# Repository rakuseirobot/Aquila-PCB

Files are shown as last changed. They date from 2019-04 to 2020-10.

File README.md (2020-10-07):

# Aquila-PCB
Aquilaの2019年度、2018年度、回路図及びボード図です。

Robocup Junior Rescue Maze Program

このリポジトリは2019年度のAquilaのメインプログラムです。

# Note

メイン基板のデータです。

/2018以下のAquila-2018-Under基板にセンサーを配線し、メイン基板に配線します。

# Link

[About robot](https://qiita.com/Shunk_/items/b6b5c49862ec9f9d852b)

[How to make RCJM](https://qiita.com/Shunk_/items/2ea0795d571d771d52ca)

[回路](https://github.com/rakuseirobot/Aquila-PCB)

[STM32-program](https://github.com/rakuseirobot/Aquila-2019)

[OpenMV](https://github.com/rakuseirobot/Aquila-OpenMV)

[設計図](https://github.com/rakuseirobot/Aquila-drawings)

[古いメインプログラム(ATxmega)](https://github.com/rakuseirobot/Aquila-Code-v3)

# Author

* Shun Kayaki

    Kyushu institute of Technology
    
    shun@guetan.dev

* Emile

# License

Copyright (c) 2019 Aquila
Released under the MIT license

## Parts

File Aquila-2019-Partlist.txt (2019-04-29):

Partlist

Exported from Aquila-2019-ex.brd at 2019/03/31 14:46

EAGLE Version 9.2.1 Copyright (c) 1988-2018 Autodesk, Inc.

Assembly variant: 

Part           Value                  Package                      Library               Position (mil)        Orientation

3.3C1          100u                   D/7343-31R                   rcl                   (1089.75 3078.75)     R180
3.3C2          0.1u                   C0805                        rcl                   (1163.75 2907.25)     R0
3.3REG         OKL-T_6-W12N-C         OKL-T/3-W5                   SamacSys_Parts        (1300 3900)           R90
5C1            100u                   D/7343-31R                   rcl                   (1841 3094.5)         R180
5C2            0.1u                   C0805                        rcl                   (1671 3223)           R180
5VREG          OKL-T_6-W12N-C         OKL-T/3-W5                   SamacSys_Parts        (2050 3900)           R90
8MHZ           P-08669_HUSG-12.000-20 HC49U-V                      Akizuki               (2625 2281.25)        R0
9C1            100u                   D/7343-31R                   rcl                   (726.25 2809)         R180
9C2            0.1u                   C0805                        rcl                   (832 3075.25)         R0
BOOT0-STM      DTS-6                  DTS-6                        forprint              (1750 662.5)          R180
C1             22uF25V                C2012                        resistor              (1476 3329)           R270
C2             10uF10V                C2012                        resistor              (1675 3355)           R180
C3             22uF25V                C2012                        resistor              (828 3284)            R0
C4             10uF10V                C2012                        resistor              (1000 3341)           R0
C5             22pF                   C1608                        resistor              (2687.5 2425)         R0
C6             22pF                   C1608                        resistor              (2562.5 2425)         R180
CHECKLED       OSTA71A1D-A            OSTA71A1D-A                  FullColorLed-forprint (1450 1787.5)         R270
CON1           XH-4                   CON4                         0@Mylibrary-main1     (3037.5 1356.25)      MR180
CON2           XH-4                   CON4                         0@Mylibrary-main1     (3037.5 1143.75)      MR180
DIO0-JP        BOOT0                  SJ                           jumper                (312.5 856.25)        R90
DIO1-JP        NRST                   SJ                           jumper                (406.25 856.25)       R90
ERROR1-R       330                    R0805                        0@Mylibrary-main1     (950 2400)            MR90
ERROR2-R       330                    R0805                        0@Mylibrary-main1     (950 2100)            MR90
FET1           IRF740                 TO220BV                      transistor-power      (2532 3634)           R0
FET1-R1        100                    R0805                        0@Mylibrary-main1     (2512 3384)           R270
FET1-R2        4.7K                   R0805                        0@Mylibrary-main1     (2432 3384)           R90
FET2           IRF740                 TO220BV                      transistor-power      (3380.5 3722.25)      R180
FET2-R1        100                    R0805                        0@Mylibrary-main1     (3405.75 3652.75)     R270
FET2-R2        4.7K                   R0805                        0@Mylibrary-main1     (3482 3652.75)        R90
GND-CH         GND                    SMD2,54-5,08                 wirepad               (400 1200)            R180
GND-CHK        GND                    2,15/1,0                     wirepad               (1400 1000)           R0
GND-CHK1       GND                    2,15/1,0                     wirepad               (1150 2650)           R0
IC1            STM32F429VGT           LQFP100                      micro-stm_v3          (2600 1800)           R180
IC2            ULN2003AN              DIL16                        ULN2003A              (1750 2500)           R90
IC3            AT24CP                 DIL08                        atmel                 (2150 2500)           R270
IC4            AE-AQM0802             AE-AQM0802                   AE-AQM0802            (3418.75 2931.25)     R90
IIC-R          XH-4                   CON4                         0@Mylibrary-main1     (1350 1300)           R180
INDILED1       330                    R0805                        0@Mylibrary-main1     (1200 2150)           R180
INDILED2       330                    R0805                        0@Mylibrary-main1     (1200 2250)           R180
INDILED3       330                    R0805                        0@Mylibrary-main1     (1200 2350)           R180
INDILED4       330                    R0805                        0@Mylibrary-main1     (1200 2450)           R180
J1             XH-5                   CON5                         0@Mylibrary-main1     (1450 2250)           MR90
JY901          XH-4                   CON4                         0@Mylibrary-main1     (1531.25 1525)        R180
L3             E1                     LED5MM                       0led                  (1000 2500)           R180
L4             E2                     LED5MM                       0led                  (1000 2200)           R180
LED1           OSL10564-CD4026B-R     DIPS1524W50P254L1260H800Q10N OSL10564-CD4026B-R    (3337.5 637.5)        R180
LED2           OSL10564-CD4026B-R     DIPS1524W50P254L1260H800Q10N OSL10564-CD4026B-R    (3337.5 118.75)       R180
LEDSP          MAIN                   AK500/2                      con-ptr500            (2541 3779)           R0
LEDSP2         MAIN                   AK500/2                      con-ptr500            (2946 3779)           R0
M-SW           TL36PO                 TL3XPO                       switch                (600 1200)            R180
MAIN-SPL       XH-2                   CON2                         forprint              (550 2100)            MR180
MAINSW2        MAIN                   MA03-1                       0con-lstb             (243 2718)            R90
MOTORDRIVER    MDCON                  ML14                         0con-harting-ml       (2050 1250)           MR0
Q3             IRF9530                TO220BV                      transistor-power      (550 3300)            R0
Q4             IRF9530                TO220BV                      transistor-power      (355 1725)            R90
Q5             IRF9530                TO220BV                      transistor-power      (550 3100)            R0
R-B            ?                      R0805                        0@Mylibrary-main1     (1700 1750)           MR0
R-G            ?                      R0805                        0@Mylibrary-main1     (1700 1850)           MR0
R-R            ?                      R0805                        0@Mylibrary-main1     (1700 1950)           MR0
R1             1.2k                   0204/7                       resistor              (1858 3291)           R0
R2             1.2k                   0204/7                       resistor              (1143 3262)           R0
RESET-STM      DTS-6                  DTS-6                        forprint              (1750 925)            R180
S1             SKRPACE010             SW_SKRPACE010                SKRPACE010            (1475 475)            R180
S2             VM                     M251                         switch                (2461 3160)           R180
S3             SKRPACE010             SW_SKRPACE010                SKRPACE010            (3568.75 500)         R180
SG1            F/EE17P                F/EE17P                      buzzer                (932 1702)            R270
SL-R1          1K                     R0805                        0@Mylibrary-main1     (2096 3251)           R270
SP-LED                                CHIPLED_0805                 led                   (2096 3090)           R0
SP-R1          1.2k                   R0805                        0@Mylibrary-main1     (2100 3800)           MR180
SP-R2          20K                    R0805                        0@Mylibrary-main1     (1395 3329)           R90
SP-R3          1.2k                   R0805                        0@Mylibrary-main1     (1350 3800)           MR180
SP-R4          20K                    R0805                        0@Mylibrary-main1     (828 3203)            R180
SP-R5          4.7K                   R0805                        0@Mylibrary-main1     (535 1420)            R90
SP-R6          4.7K                   R0805                        0@Mylibrary-main1     (412.5 2856.25)       R180
SP-RC1         20k                    RTRIM3296W                   resistor              (2200 3700)           R180
SP-RC2         20k                    RTRIM3296W                   resistor              (1450 3700)           R180
SP-SW2         219-02                 CTS-219-02                   switch-dil            (1400 2950)           R180
SPI-LCD                               FE09                         0@con-lsta            (2500 600)            R270
SPI-R          XH-6                   CON6                         0@Mylibrary-main1     (2850 2750)           R270
SRAM-R1        4.7K                   R0805                        0@Mylibrary-main1     (2474 2524.5)         R270
SRAM-R2        10k                    R0805                        0@Mylibrary-main1     (2412.5 2700)         R180
STEPINDI1      LED                    CHIPLED_0805                 led                   (1350 2150)           R270
STEPINDI2      LED                    CHIPLED_0805                 led                   (1350 2250)           R270
STEPINDI3      LED                    CHIPLED_0805                 led                   (1350 2350)           R270
STEPINDI4      LED                    CHIPLED_0805                 led                   (1350 2450)           R270
STM-C1         0.1u                   C0805                        rcl                   (2250 2112.5)         R0
STM-C2         0.1u                   C0805                        rcl                   (2950 2150)           R270
STM-C3         0.1u                   C0805                        rcl                   (2275 1462.5)         R90
STM-C4         0.1u                   C0805                        rcl                   (3037.5 1556.25)      R180
STM-C5         0.1u                   C0805                        rcl                   (3037.5 1487.5)       R0
STM-C6         0.1u                   C0805                        rcl                   (2175 1587.5)         MR0
STM-R1         4.7K                   R0805                        0@Mylibrary-main1     (1950 975)            R270
STM-R2         4.7K                   R0805                        0@Mylibrary-main1     (1950 712.5)          R270
SUOPPLY-SW2    XH-3                   CON3                         forprint              (532.25 2587.25)      MR180
SUPPLY3.3V     MAIN                   AK500/2                      con-ptr500            (150 1800)            R270
SUPPLY5V       MAIN                   AK500/2                      con-ptr500            (150 2200)            R270
SUPPLY9        MAIN                   AK500/2                      con-ptr500            (150 3200)            R270
SV1                                   MA06-1                       0con-lstb             (2050 750)            R90
TESTSW-R1      4.7K                   R0805                        0@Mylibrary-main1     (1424.5 446.5)        MR270
TESTSW-R2      4.7K                   R0805                        0@Mylibrary-main1     (1774 446)            MR270
TESTSW-R3      4.7K                   R0805                        0@Mylibrary-main1     (2125 446)            MR270
TO-UNDER                              ML26                         0con-harting-ml       (3593.75 1437.5)      MR270
TOUCH1         XH-3                   CON3                         forprint              (2500 2900)           MR90
TOUCH2         XH-3                   CON3                         forprint              (2250 2900)           MR90
TW-SP          XH-2                   CON2                         0@Mylibrary-main1     (1450 750)            R90
TWILITE        C2                     MA05-1                       con-lstb-forprint     (1129 1114)           R0
U$2            5566-04A               5566-04A                     con-molex             (196 1303)            MR180
U2             23K256-I/SN            SOIC127P600X175-8N           23K256-I_SN           (2625 2637.5)         R90
VOLTAGE-METER1 XH-2                   CON2                         forprint              (996.5 2811.25)       MR270
VOLTAGE-METER2 XH-2                   CON2                         forprint              (2200 3400)           MR0
X-R2           4.7K                   R0805                        0@Mylibrary-main1     (932 1761)            MR90
X2             DCJACK-MJ179P          MJ-179P                      kamiki-dcjack         (550 3550)            R270
XB1            XBEE-PRO               XBEE-PRO                     maxstream             (650 550)             R90
XBEE-RST       4.7K                   R0805                        0@Mylibrary-main1     (1231.25 550)         R90
XMEGA-TEST1    SW1                    DTS-6                        forprint              (1552.5 237.5)        R180
XMEGA-TEST2    SW2                    DTS-6                        forprint              (1902.5 237.5)        R180
XMEGA-TEST3    SW3                    DTS-6                        forprint              (2252.5 237.5)        R180

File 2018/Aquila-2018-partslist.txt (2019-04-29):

Partlist

Exported from Aquila-2018.sch at 2018/07/30 12:54

EAGLE Version 9.1.1 Copyright (c) 1988-2018 Autodesk, Inc.

Assembly variant: 

Part           Value          Device                     Package            Library                    Sheet

3.3C1          100u           CPOL-USE2.5-6              E2,5-6             rcl                        1
3.3C2          0.1u           C-EUC0805                  C0805              rcl                        1
3.3REG         OKL-T_6-W12N-C OKL-T_6-W12N-C             OKL-T/3-W5         SamacSys_Parts             1
5C1            100u           CPOL-USE2.5-6              E2,5-6             rcl                        1
5C2            0.1u           C-EUC0805                  C0805              rcl                        1
5VREG          OKL-T_6-W12N-C OKL-T_6-W12N-C             OKL-T/3-W5         SamacSys_Parts             1
9C1            100u           CPOL-USE2.5-6              E2,5-6             rcl                        1
9C2            0.1u           C-EUC0805                  C0805              rcl                        1
C1             22uF25V        C-EUC2012                  C2012              resistor                   1
C2             10uF10V        C-EUC2012                  C2012              resistor                   1
C3             22uF25V        C-EUC2012                  C2012              resistor                   1
C4             10uF10V        C-EUC2012                  C2012              resistor                   1
CHECKLED       OSTA71A1D-A    OSTA71A1D-A                OSTA71A1D-A        FullColorLed-forprint      1
ERROR1-R       330            R-US_R0805                 R0805              0@Mylibrary-main1          1
ERROR2-R       330            R-US_R0805                 R0805              0@Mylibrary-main1          1
FT-POWERLED                   LEDCHIPLED_0805            CHIPLED_0805       led                        1
FT232-R8       330            R-US_R0805                 R0805              0@Mylibrary-main1          1
FT232-R9       330            R-US_R0805                 R0805              0@Mylibrary-main1          1
FT232-R10      4.7K           R-US_R0805                 R0805              0@Mylibrary-main1          1
FT232-R11      10K            R-US_R0805                 R0805              0@Mylibrary-main1          1
FT232-R12      1K             R-US_R0805                 R0805              0@Mylibrary-main1          1
FT232-R13      23             R-US_R0805                 R0805              0@Mylibrary-main1          1
FT232-R14      23             R-US_R0805                 R0805              0@Mylibrary-main1          1
FT232USBCON    Wrie-USB       MINI-USB-SCHIELD-32005-201 32005-201          con-cypressindustries      1
GND-CH                        SMD5                       SMD2,54-5,08       wirepad                    1
GND-CHK                       2,15/1,0                   2,15/1,0           wirepad                    1
GND-CHK1                      2,15/1,0                   2,15/1,0           wirepad                    1
I2C-R          XH-4           XH-4                       CON4               0@Mylibrary-main1          1
IC1            FT232RL        FT232RL                    SSOP28             ftdichip                   1
IC2            ULN2003AN      ULN2003AN                  DIL16              ULN2003A                   1
INDILED1       330            R-US_R0805                 R0805              0@Mylibrary-main1          1
INDILED2       330            R-US_R0805                 R0805              0@Mylibrary-main1          1
INDILED3       330            R-US_R0805                 R0805              0@Mylibrary-main1          1
INDILED4       330            R-US_R0805                 R0805              0@Mylibrary-main1          1
J1             XH-5           XH-5                       CON5               0@Mylibrary-main1          1
JTAG                          20021221-00010C4LF         20021221-00010C4LF fci                        1
L3             E1             LED5MM                     LED5MM             0led                       1
L4             E2             LED5MM                     LED5MM             0led                       1
L5             RXDLED         LEDCHIPLED_0805            CHIPLED_0805       led                        1
L6             TXDLED         LEDCHIPLED_0805            CHIPLED_0805       led                        1
LCD            C2             MA05-1                     MA05-1             con-lstb-forprint          1
M-SW           TL36PO         TL36PO                     TL3XPO             switch                     1
M1-R1          4.7K           R-US_R0805                 R0805              0@Mylibrary-main1          1
M2-R1          4.7K           R-US_R0805                 R0805              0@Mylibrary-main1          1
MAIN-SPL       XH-2           XH-2                       CON2               forprint                   1
MAINSW2                       MA03-1                     MA03-1             0con-lstb                  1
MEGA1                         MEGA8-AI                   TQFP32-08          atmel                      1
MEGA1-C1       0.1u           C-EUC0805                  C0805              rcl                        1
MEGA2                         MEGA8-AI                   TQFP32-08          atmel                      1
MEGA2-C1       0.1u           C-EUC0805                  C0805              rcl                        1
MOTORDRIVER                   ML14                       ML14               0con-harting-ml            1
MPU            XH-4           XH-4                       CON4               0@Mylibrary-main1          1
Q1             20MHz          CSTLS_X                    CSTLS_X            0Murata-ceralocks-forprint 1
Q2             20MHz          CSTLS_X                    CSTLS_X            0Murata-ceralocks-forprint 1
Q3             IRF9530        IRF9530                    TO220BV            transistor-power           1
Q4             IRF9530        IRF9530                    TO220BV            transistor-power           1
Q5             IRF9530        IRF9530                    TO220BV            transistor-power           1
R-B            ?              R-US_R0805                 R0805              0@Mylibrary-main1          1
R-G            ?              R-US_R0805                 R0805              0@Mylibrary-main1          1
R-R            ?              R-US_R0805                 R0805              0@Mylibrary-main1          1
R1             1.2k           R-EU_0204/7                0204/7             resistor                   1
R2             1.2k           R-EU_0204/7                0204/7             resistor                   1
RESET-MEGA1    R-1            DTS-6                      DTS-6              forprint                   1
RESET-MEGA2    R-2            DTS-6                      DTS-6              forprint                   1
RESET-XMEGA    DTS-6          DTS-6                      DTS-6              forprint                   1
S1                            DIP08S                     DIP08S             switch-dil-forprint        1
S2                            M251                       M251               switch                     1
SG1            F/EE17P        F/EE17P                    F/EE17P            buzzer                     1
SL-R1          1K             R-US_R0805                 R0805              0@Mylibrary-main1          1
SP-LED                        LEDCHIPLED_0805            CHIPLED_0805       led                        1
SP-R1          1.2k           R-US_R0805                 R0805              0@Mylibrary-main1          1
SP-R2          20K            R-US_R0805                 R0805              0@Mylibrary-main1          1
SP-R3          1.2k           R-US_R0805                 R0805              0@Mylibrary-main1          1
SP-R4          20K            R-US_R0805                 R0805              0@Mylibrary-main1          1
SP-R5          4.7K           R-US_R0805                 R0805              0@Mylibrary-main1          1
SP-R6          4.7K           R-US_R0805                 R0805              0@Mylibrary-main1          1
SP-RC1         20k            R-TRIMM3296W               RTRIM3296W         resistor                   1
SP-RC2         20k            R-TRIMM3296W               RTRIM3296W         resistor                   1
SP-SW2         219-02         219-02                     CTS-219-02         switch-dil                 1
SPI-R          XH-6           XH-6                       CON6               0@Mylibrary-main1          1
SPI-SW                        DIP03YL                    DIP03YL            switch-dil                 1
SRAM-R1        4.7K           R-US_R0805                 R0805              0@Mylibrary-main1          1
SRAM-R2        10k            R-US_R0805                 R0805              0@Mylibrary-main1          1
SS-R1          4.7K           R-US_R0805                 R0805              0@Mylibrary-main1          1
SS-R2          4.7K           R-US_R0805                 R0805              0@Mylibrary-main1          1
STEPINDI1      LED            LEDCHIPLED_0805            CHIPLED_0805       led                        1
STEPINDI2      LED            LEDCHIPLED_0805            CHIPLED_0805       led                        1
STEPINDI3      LED            LEDCHIPLED_0805            CHIPLED_0805       led                        1
STEPINDI4      KED            LEDCHIPLED_0805            CHIPLED_0805       led                        1
SUOPPLY-SW2    XH-3           XH-3                       CON3               forprint                   1
SUPPLY3.3V     MAIN           AK500/2                    AK500/2            con-ptr500                 1
SUPPLY5V       MAIN           AK500/2                    AK500/2            con-ptr500                 1
SUPPLY9        MAIN           AK500/2                    AK500/2            con-ptr500                 1
SV1                           ML6                        ML6                con-harting-ml             1
TESTSW-R1      4.7K           R-US_R0805                 R0805              0@Mylibrary-main1          1
TESTSW-R2      4.7K           R-US_R0805                 R0805              0@Mylibrary-main1          1
TESTSW-R3      4.7K           R-US_R0805                 R0805              0@Mylibrary-main1          1
TO-UNDER                      ML26                       ML26               0con-harting-ml            1
TOUCH1         XH-3           XH-3                       CON3               forprint                   1
TOUCH2         XH-3           XH-3                       CON3               forprint                   1
TW-SP          XH-2           XH-2                       CON2               0@Mylibrary-main1          1
TWILITE        C2             MA05-1                     MA05-1             con-lstb-forprint          1
U$2            5566-04A       5566-04A                   5566-04A           con-molex                  1
U1                            ATXMEGA128A1U-AU           TQFP-100A-100      atmel-xmega                1
U2             23K256-I/SN    23K256-I/SN                SOIC127P600X175-8N 23K256-I_SN                1
VOLTAGE-METER1 XH-2           XH-2                       CON2               forprint                   1
VOLTAGE-METER2 XH-2           XH-2                       CON2               forprint                   1
X-R1           4.7K           R-US_R0805                 R0805              0@Mylibrary-main1          1
X-R2           4.7K           R-US_R0805                 R0805              0@Mylibrary-main1          1
X2             DCJACK-MJ179P  DCJACK-MJ179P              MJ-179P            kamiki-dcjack              1
XMEGA-C1       0.1u           C-EUC0805                  C0805              rcl                        1
XMEGA-C2       0.1u           C-EUC0805                  C0805              rcl                        1
XMEGA-TEST1    SW1            DTS-6                      DTS-6              forprint                   1
XMEGA-TEST2    SW2            DTS-6                      DTS-6              forprint                   1
XMEGA-TEST3    SW3            DTS-6                      DTS-6              forprint                   1

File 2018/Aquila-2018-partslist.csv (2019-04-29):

Part | Value | Device | Package | Library | Sheet
JTAG |  | 20021221-00010C4LF | 20021221-00010C4LF | fci | 1
SP-SW2 | 219-02 | 219-02 | CTS-219-02 | switch-dil | 1
U2 | 23K256-I/SN | 23K256-I/SN | SOIC127P600X175-8N | 23K256-I_SN | 1
U$2 | 5566-04A | 5566-04A | 5566-04A | con-molex | 1
SUPPLY3.3V | MAIN | AK500/2 | AK500/2 | con-ptr500 | 1
SUPPLY5V | MAIN | AK500/2 | AK500/2 | con-ptr500 | 1
SUPPLY9 | MAIN | AK500/2 | AK500/2 | con-ptr500 | 1
U1 |  | ATXMEGA128A1U-AU | TQFP-100A-100 | atmel-xmega | 1
3.3C2 | 0.1u | C-EUC0805 | C0805 | rcl | 1
5C2 | 0.1u | C-EUC0805 | C0805 | rcl | 1
9C2 | 0.1u | C-EUC0805 | C0805 | rcl | 1
MEGA1-C1 | 0.1u | C-EUC0805 | C0805 | rcl | 1
MEGA2-C1 | 0.1u | C-EUC0805 | C0805 | rcl | 1
XMEGA-C1 | 0.1u | C-EUC0805 | C0805 | rcl | 1
XMEGA-C2 | 0.1u | C-EUC0805 | C0805 | rcl | 1
C1 | 22uF25V | C-EUC2012 | C2012 | resistor | 1
C2 | 10uF10V | C-EUC2012 | C2012 | resistor | 1
C3 | 22uF25V | C-EUC2012 | C2012 | resistor | 1
C4 | 10uF10V | C-EUC2012 | C2012 | resistor | 1
3.3C1 | 100u | CPOL-USE2.5-6 | E2 |  | 1
5C1 | 100u | CPOL-USE2.5-6 | E2 |  | 1
9C1 | 100u | CPOL-USE2.5-6 | E2 |  | 1
Q1 | 20MHz | CSTLS_X | CSTLS_X | 0Murata-ceralocks-forprint | 1
Q2 | 20MHz | CSTLS_X | CSTLS_X | 0Murata-ceralocks-forprint | 1
X2 | DCJACK-MJ179P | DCJACK-MJ179P | MJ-179P | kamiki-dcjack | 1
SPI-SW |  | DIP03YL | DIP03YL | switch-dil | 1
S1 |  | DIP08S | DIP08S | switch-dil-forprint | 1
RESET-MEGA1 | R-1 | DTS-6 | DTS-6 | forprint | 1
RESET-MEGA2 | R-2 | DTS-6 | DTS-6 | forprint | 1
RESET-XMEGA | DTS-6 | DTS-6 | DTS-6 | forprint | 1
XMEGA-TEST1 | SW1 | DTS-6 | DTS-6 | forprint | 1
XMEGA-TEST2 | SW2 | DTS-6 | DTS-6 | forprint | 1
XMEGA-TEST3 | SW3 | DTS-6 | DTS-6 | forprint | 1
SG1 | F/EE17P | F/EE17P | F/EE17P | buzzer | 1
IC1 | FT232RL | FT232RL | SSOP28 | ftdichip | 1
Q3 | IRF9530 | IRF9530 | TO220BV | transistor-power | 1
Q4 | IRF9530 | IRF9530 | TO220BV | transistor-power | 1
Q5 | IRF9530 | IRF9530 | TO220BV | transistor-power | 1
L3 | E1 | LED5MM | LED5MM | 0led | 1
L4 | E2 | LED5MM | LED5MM | 0led | 1
FT-POWERLED |  | LEDCHIPLED_0805 | CHIPLED_0805 | led | 1
L5 | RXDLED | LEDCHIPLED_0805 | CHIPLED_0805 | led | 1
L6 | TXDLED | LEDCHIPLED_0805 | CHIPLED_0805 | led | 1
SP-LED |  | LEDCHIPLED_0805 | CHIPLED_0805 | led | 1
STEPINDI1 | LED | LEDCHIPLED_0805 | CHIPLED_0805 | led | 1
STEPINDI2 | LED | LEDCHIPLED_0805 | CHIPLED_0805 | led | 1
STEPINDI3 | LED | LEDCHIPLED_0805 | CHIPLED_0805 | led | 1
STEPINDI4 | KED | LEDCHIPLED_0805 | CHIPLED_0805 | led | 1
S2 |  | M251 | M251 | switch | 1
MAINSW2 |  | MA03-1 | MA03-1 | 0con-lstb | 1
LCD | C2 | MA05-1 | MA05-1 | con-lstb-forprint | 1
TWILITE | C2 | MA05-1 | MA05-1 | con-lstb-forprint | 1
MEGA2 |  | MEGA8-AI | TQFP32-08 | atmel | 1
MEGA1 |  | MEGA8-AI | TQFP32-08 | atmel | 1
FT232USBCON | Wrie-USB | MINI-USB-SCHIELD-32005-201 | 32005-201 | con-cypressindustries | 1
MOTORDRIVER |  | ML14 | ML14 | 0con-harting-ml | 1
TO-UNDER |  | ML26 | ML26 | 0con-harting-ml | 1
SV1 |  | ML6 | ML6 | con-harting-ml | 1
3.3REG | OKL-T_6-W12N-C | OKL-T_6-W12N-C | OKL-T/3-W5 | SamacSys_Parts | 1
5VREG | OKL-T_6-W12N-C | OKL-T_6-W12N-C | OKL-T/3-W5 | SamacSys_Parts | 1
CHECKLED | OSTA71A1D-A | OSTA71A1D-A | OSTA71A1D-A | FullColorLed-forprint | 1
R1 | 1.2k | R-EU_0204/7 | 0204/7 | resistor | 1
R2 | 1.2k | R-EU_0204/7 | 0204/7 | resistor | 1
SP-RC1 | 20k | R-TRIMM3296W | RTRIM3296W | resistor | 1
SP-RC2 | 20k | R-TRIMM3296W | RTRIM3296W | resistor | 1
ERROR1-R | 330 | R-US_R0805 | R0805 | 0@Mylibrary-main1 | 1
ERROR2-R | 330 | R-US_R0805 | R0805 | 0@Mylibrary-main1 | 1
FT232-R8 | 330 | R-US_R0805 | R0805 | 0@Mylibrary-main1 | 1
FT232-R9 | 330 | R-US_R0805 | R0805 | 0@Mylibrary-main1 | 1
FT232-R10 | 4.7K | R-US_R0805 | R0805 | 0@Mylibrary-main1 | 1
FT232-R11 | 10K | R-US_R0805 | R0805 | 0@Mylibrary-main1 | 1
FT232-R12 | 1K | R-US_R0805 | R0805 | 0@Mylibrary-main1 | 1
FT232-R13 | 23 | R-US_R0805 | R0805 | 0@Mylibrary-main1 | 1
FT232-R14 | 23 | R-US_R0805 | R0805 | 0@Mylibrary-main1 | 1
INDILED1 | 330 | R-US_R0805 | R0805 | 0@Mylibrary-main1 | 1
INDILED2 | 330 | R-US_R0805 | R0805 | 0@Mylibrary-main1 | 1
INDILED3 | 330 | R-US_R0805 | R0805 | 0@Mylibrary-main1 | 1
INDILED4 | 330 | R-US_R0805 | R0805 | 0@Mylibrary-main1 | 1
M1-R1 | 4.7K | R-US_R0805 | R0805 | 0@Mylibrary-main1 | 1
M2-R1 | 4.7K | R-US_R0805 | R0805 | 0@Mylibrary-main1 | 1
R-B | ? | R-US_R0805 | R0805 | 0@Mylibrary-main1 | 1
R-G | ? | R-US_R0805 | R0805 | 0@Mylibrary-main1 | 1
R-R | ? | R-US_R0805 | R0805 | 0@Mylibrary-main1 | 1
SL-R1 | 1K | R-US_R0805 | R0805 | 0@Mylibrary-main1 | 1
SP-R1 | 1.2k | R-US_R0805 | R0805 | 0@Mylibrary-main1 | 1
SP-R2 | 20K | R-US_R0805 | R0805 | 0@Mylibrary-main1 | 1
SP-R3 | 1.2k | R-US_R0805 | R0805 | 0@Mylibrary-main1 | 1
SP-R4 | 20K | R-US_R0805 | R0805 | 0@Mylibrary-main1 | 1
SP-R5 | 4.7K | R-US_R0805 | R0805 | 0@Mylibrary-main1 | 1
SP-R6 | 4.7K | R-US_R0805 | R0805 | 0@Mylibrary-main1 | 1
SRAM-R1 | 4.7K | R-US_R0805 | R0805 | 0@Mylibrary-main1 | 1
SRAM-R2 | 10k | R-US_R0805 | R0805 | 0@Mylibrary-main1 | 1
SS-R1 | 4.7K | R-US_R0805 | R0805 | 0@Mylibrary-main1 | 1
SS-R2 | 4.7K | R-US_R0805 | R0805 | 0@Mylibrary-main1 | 1
TESTSW-R1 | 4.7K | R-US_R0805 | R0805 | 0@Mylibrary-main1 | 1
TESTSW-R2 | 4.7K | R-US_R0805 | R0805 | 0@Mylibrary-main1 | 1
TESTSW-R3 | 4.7K | R-US_R0805 | R0805 | 0@Mylibrary-main1 | 1
X-R1 | 4.7K | R-US_R0805 | R0805 | 0@Mylibrary-main1 | 1
X-R2 | 4.7K | R-US_R0805 | R0805 | 0@Mylibrary-main1 | 1
GND-CH | SMD5 | SMD2 |  |  | 1
M-SW | TL36PO | TL36PO | TL3XPO | switch | 1
IC2 | ULN2003AN | ULN2003AN | DIL16 | ULN2003A | 1
MAIN-SPL | XH-2 | XH-2 | CON2 | forprint | 1
TW-SP | XH-2 | XH-2 | CON2 | 0@Mylibrary-main1 | 1
VOLTAGE-METER1 | XH-2 | XH-2 | CON2 | forprint | 1
VOLTAGE-METER2 | XH-2 | XH-2 | CON2 | forprint | 1
SUOPPLY-SW2 | XH-3 | XH-3 | CON3 | forprint | 1
TOUCH1 | XH-3 | XH-3 | CON3 | forprint | 1
TOUCH2 | XH-3 | XH-3 | CON3 | forprint | 1
I2C-R | XH-4 | XH-4 | CON4 | 0@Mylibrary-main1 | 1
MPU | XH-4 | XH-4 | CON4 | 0@Mylibrary-main1 | 1
J1 | XH-5 | XH-5 | CON5 | 0@Mylibrary-main1 | 1
SPI-R | XH-6 | XH-6 | CON6 | 0@Mylibrary-main1 | 1
GND-CHK | 2 |  |  |  | 1
GND-CHK1 | 2 |  |  |  | 1

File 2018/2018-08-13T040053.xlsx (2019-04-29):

索引 | 数量 | 品番 | メーカー品番 | 商品概要 | 客先参照品番 | 入手可能 | 繰越注文 | 単価 | 合計金額 JPY
1 | 4 | 497-2344-5-ND | ULN2003A | IC PWR RELAY 7NPN 1:1 16DIP |  | 4 | 0 | 67 | 268
2 | 4 | 23K256T-I/SNCT-ND | 23K256T-I/SN | IC SRAM 256K SPI 20MHZ 8SOIC |  | 4 | 0 | 135 | 540
3 | 5 | ATXMEGA128A1U-AN-ND | ATXMEGA128A1U-AN | IC MCU 8BIT 128KB FLASH 100TQFP |  | 5 | 0 | 744 | 3720
4 | 8 | S9173-ND | SBH11-PBPC-D13-ST-BK | CONN HEADER 2.54MM 26POS GOLD |  | 8 | 0 | 78 | 624
5 | 6 | S9323-ND | SFH213-PPPC-D13-ID-BK-M181 | CONN SOCKET IDC 26POS W/STR GOLD |  | 6 | 0 | 147 | 882
6 | 8 | S9170-ND | SBH11-PBPC-D07-ST-BK | CONN HEADER 2.54MM 14POS GOLD |  | 8 | 0 | 47 | 376
7 | 6 | S9307-ND | SFH213-PPPC-D07-ID-BK | CONN SOCKET IDC 14POS W/STR GOLD |  | 6 | 0 | 90 | 540
8 | 16 | 455-1662-ND | B7B-ZR(LF)(SN) | CONN HEADER ZH TOP 7POS 1.5MM |  | 16 | 0 | 38.6 | 618
9 | 25 | 455-1200-ND | ZHR-7 | CONN HOUSING ZH 7POS 1.5MM WHT |  | 25 | 0 | 15.04 | 376
10 | 40 | 455-3078-ND | ASZHSZH28K51 | JUMPER SZH-002T-P0.5 X2 2" |  | 40 | 0 | 40.4 | 1616
11 | 100 | 455-1281-1-ND | SZH-003T-P0.5 | CONN TERM CRIMP ZH 28-32AWG TIN |  | 100 | 0 | 2.44 | 244
12 | 15 | 455-2250-ND | S3B-XH-A(LF)(SN) | CONN HEADER XH SIDE 3POS 2.5MM |  | 15 | 0 | 24.1 | 362
13 | 10 | 455-2243-ND | S4B-XH-A(LF)(SN) | CONN HEADER XH SIDE 4POS 2.5MM |  | 10 | 0 | 30.4 | 304
14 | 5 | CT3114CT-ND | 219-2MSTR | SWITCH SLIDE DIP SPST 100MA 20V |  | 5 | 0 | 86 | 430
15 | 4 | CT3117CT-ND | 219-4MSTR | SWITCH SLIDE DIP SPST 100MA 20V |  | 4 | 0 | 108 | 432
16 | 6 | WM3801-ND | 0039281043 | CONN HEADER 4POS 4.2MM VERT TIN |  | 6 | 0 | 91 | 546
17 | 10 | WM3701-ND | 0039012040 | CONN RECEPT 4POS DUAL |  | 10 | 0 | 29.9 | 299
18 | 50 | WM2501CT-ND | 39-00-0038 | CONN TERM FEMALE 18-24AWG TIN |  | 50 | 0 | 6.48 | 324

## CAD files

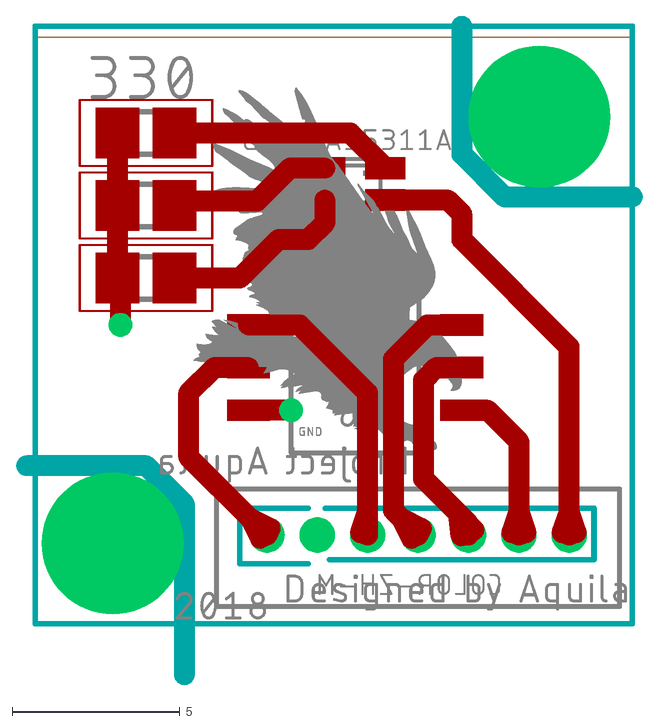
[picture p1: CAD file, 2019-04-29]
2018/Color2018.dxf
18.6 x 19.9

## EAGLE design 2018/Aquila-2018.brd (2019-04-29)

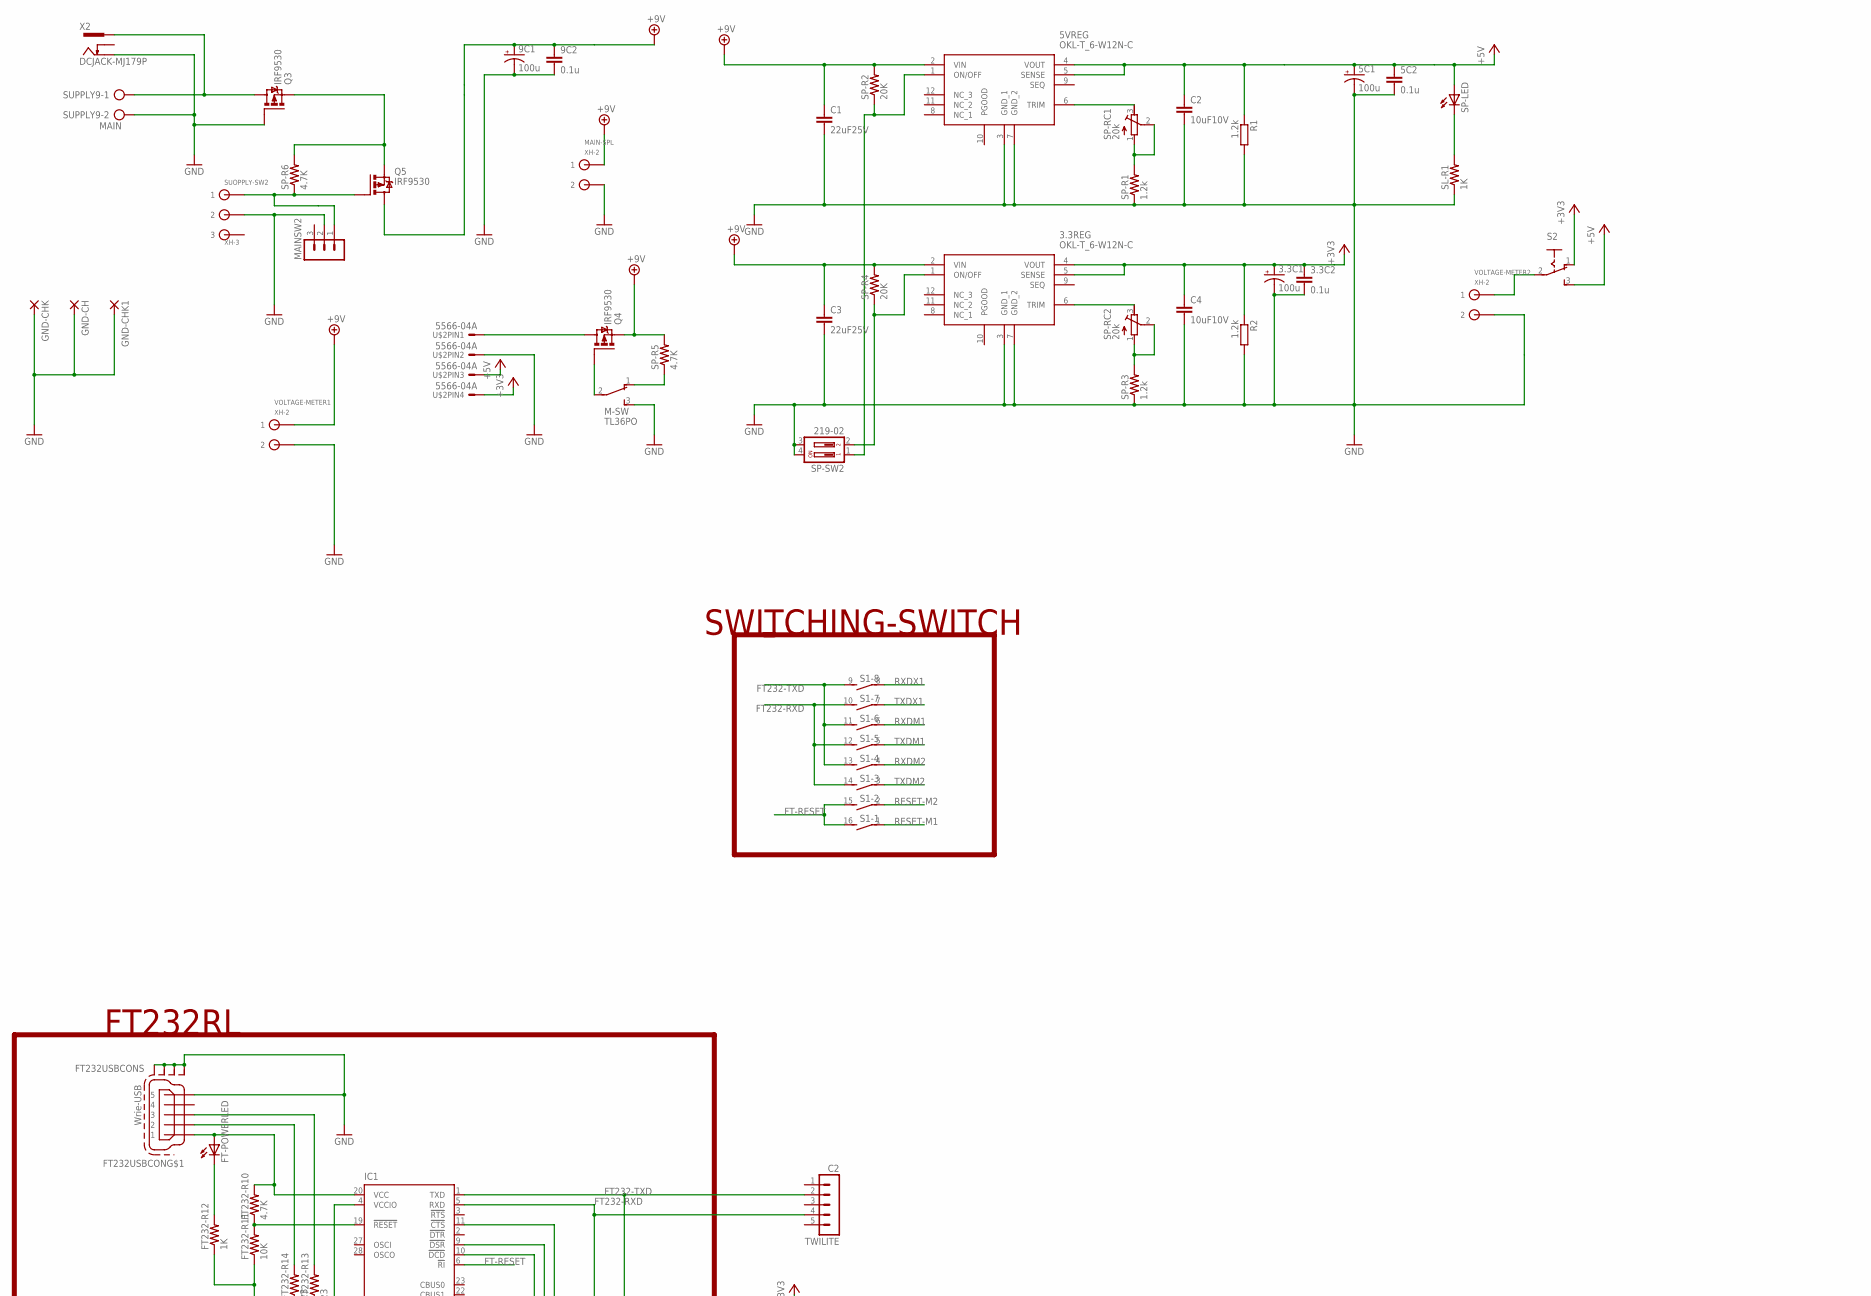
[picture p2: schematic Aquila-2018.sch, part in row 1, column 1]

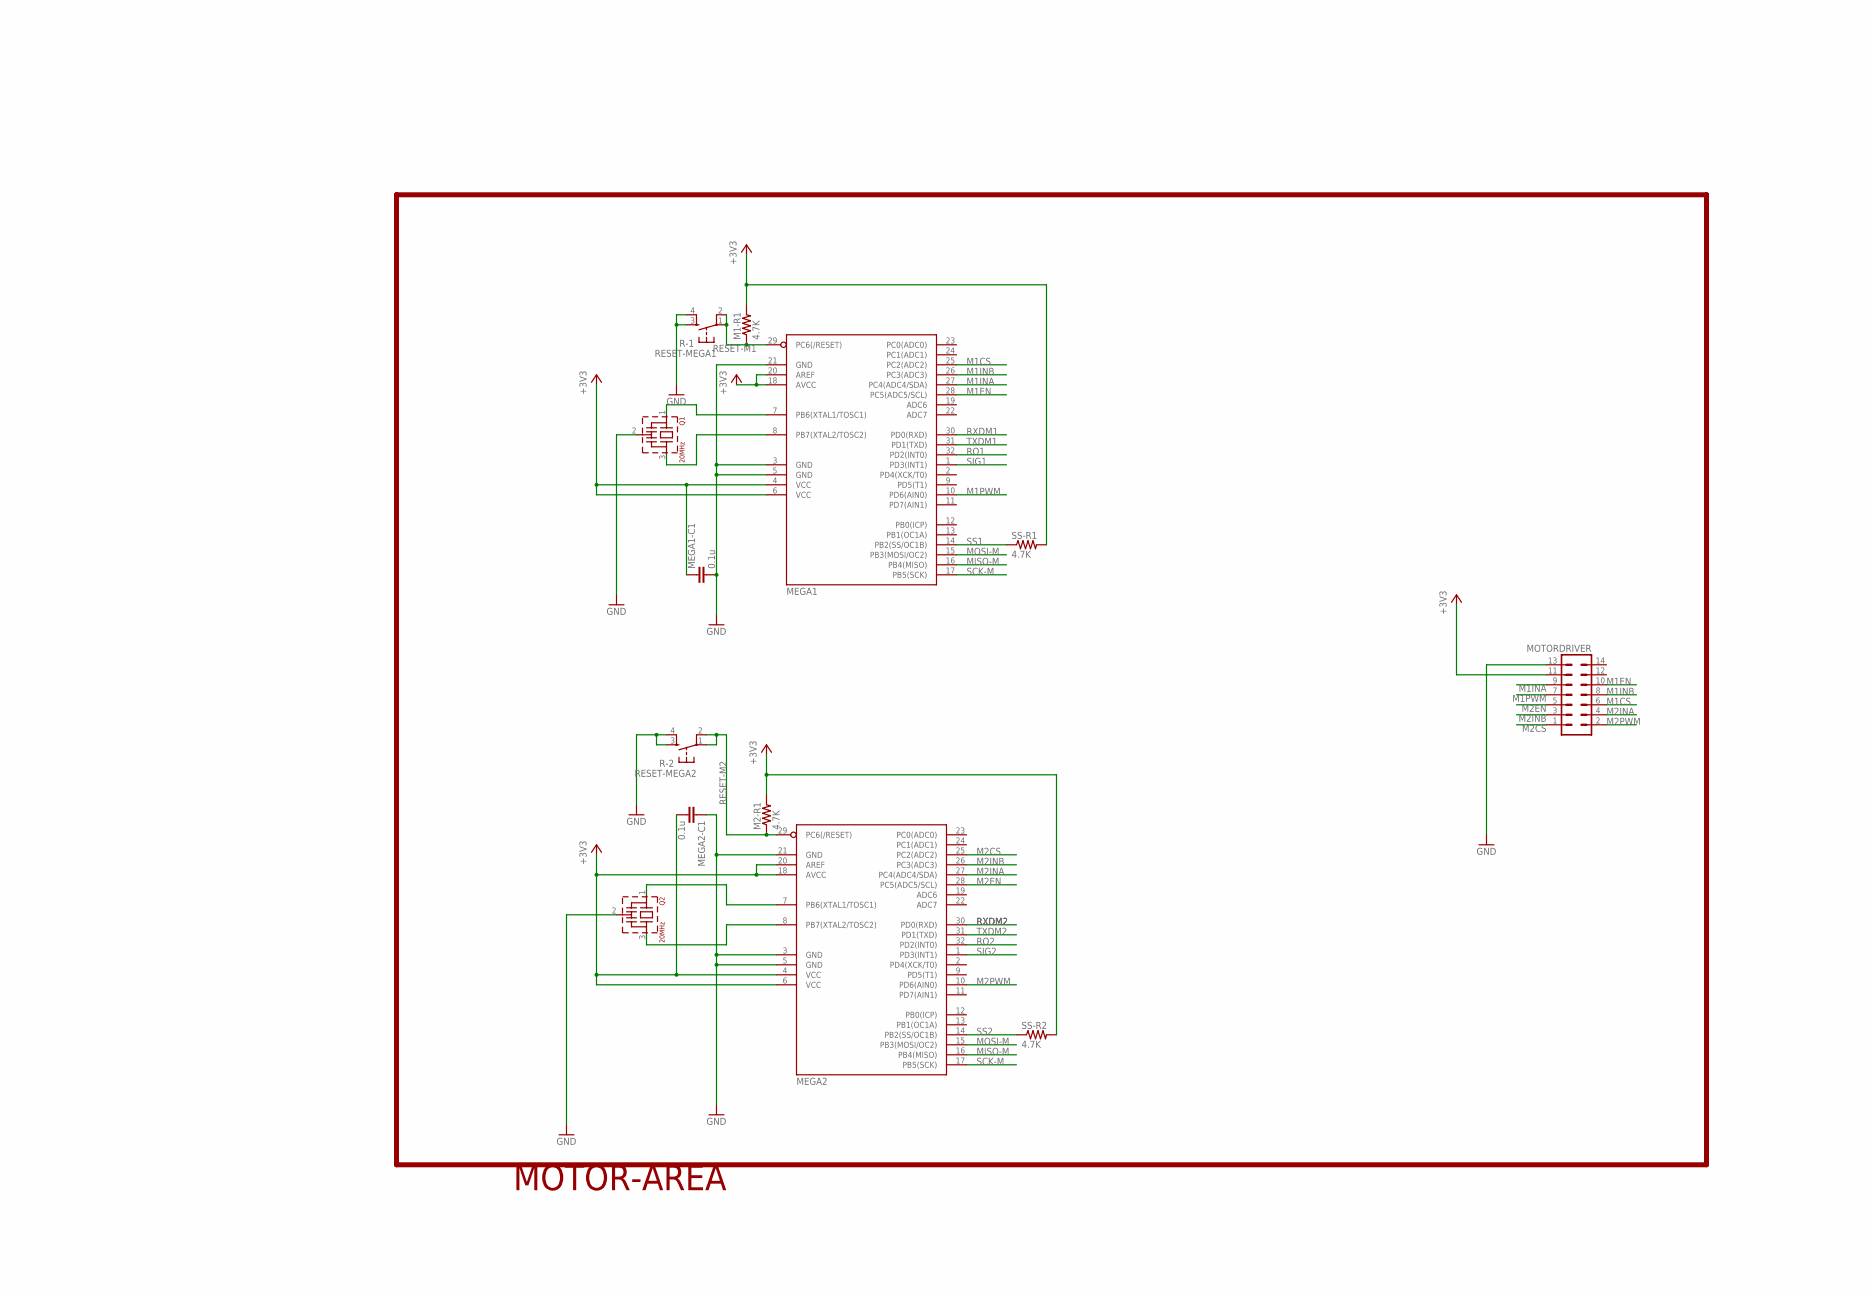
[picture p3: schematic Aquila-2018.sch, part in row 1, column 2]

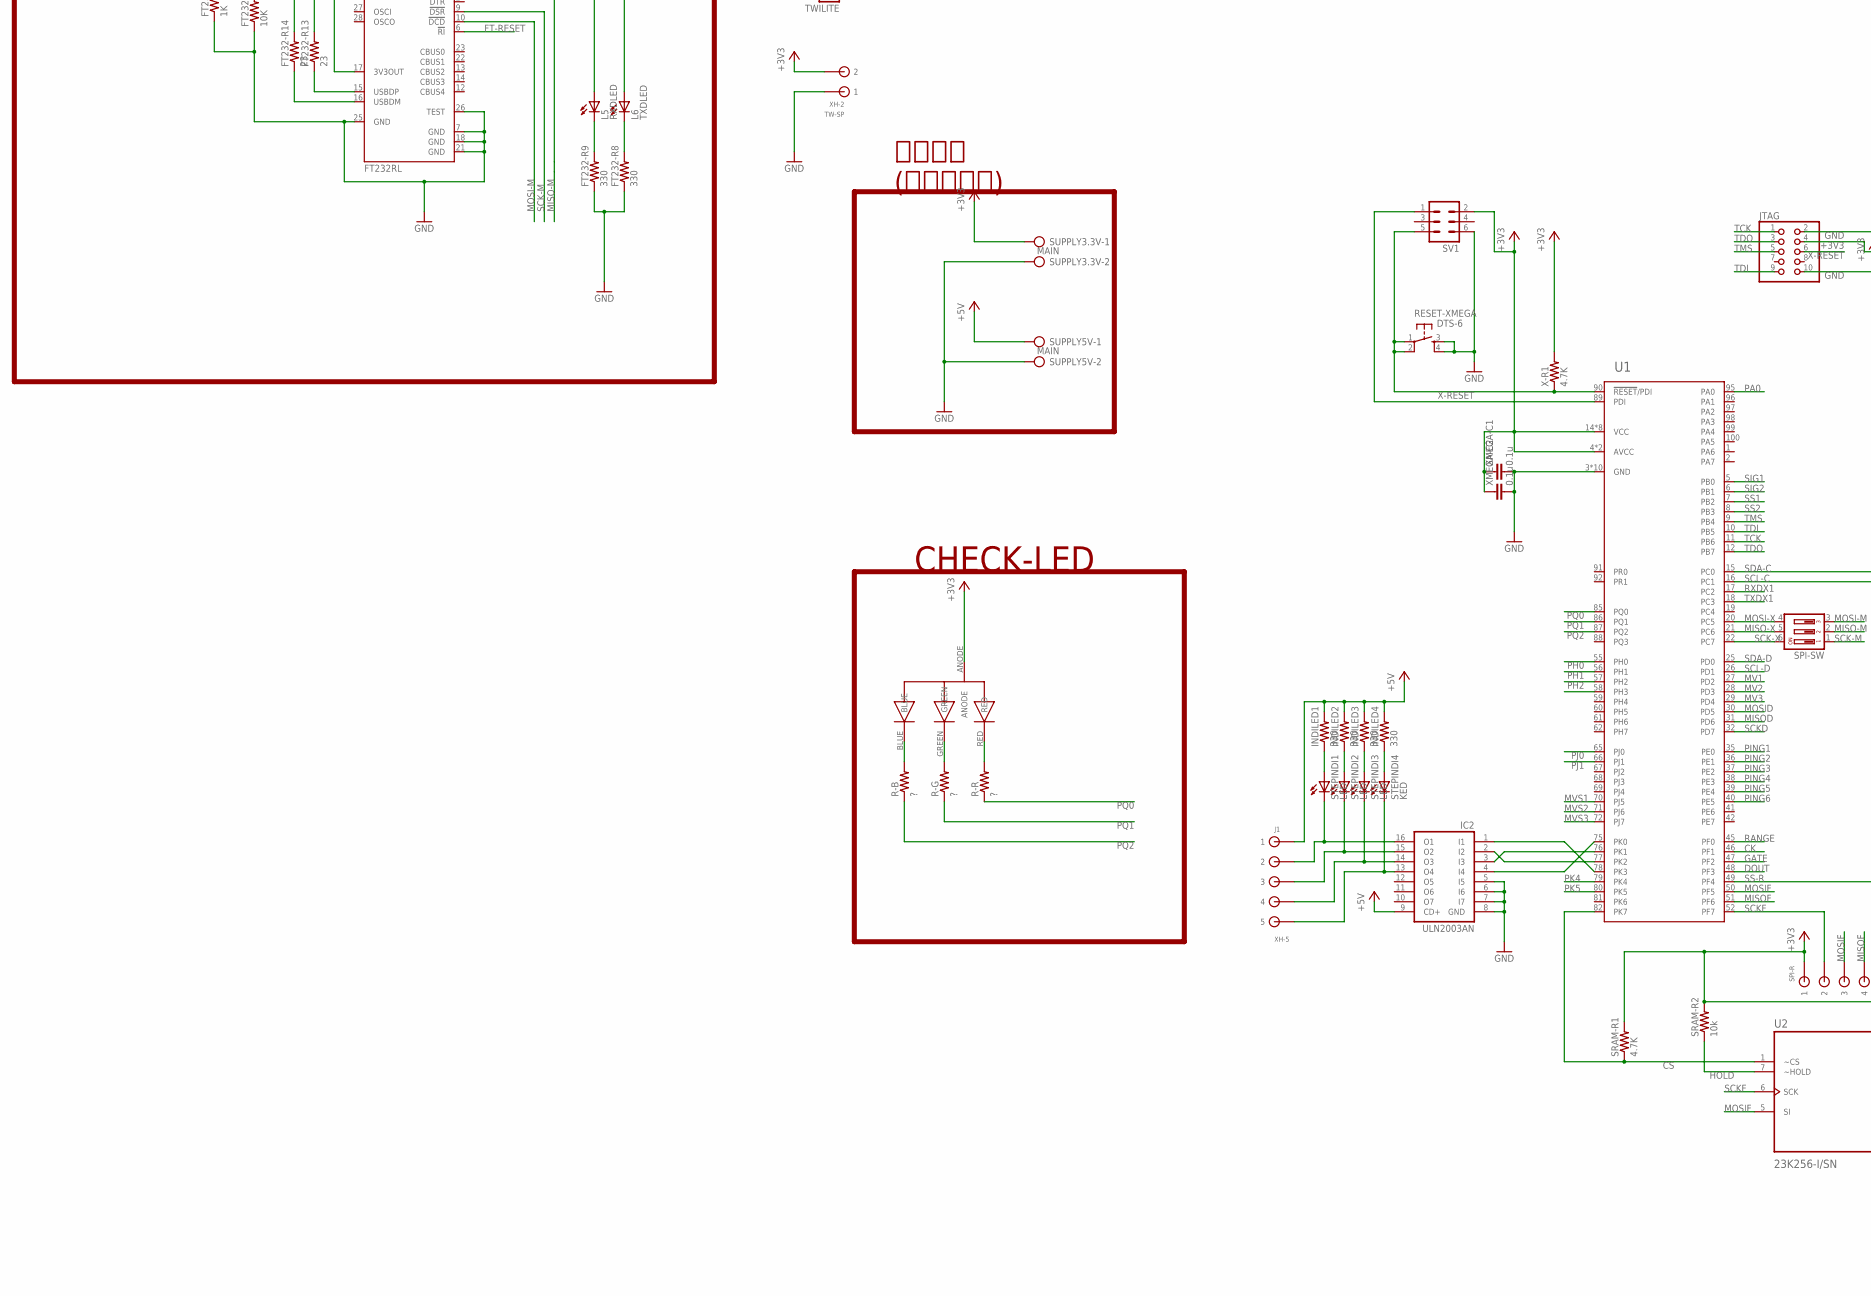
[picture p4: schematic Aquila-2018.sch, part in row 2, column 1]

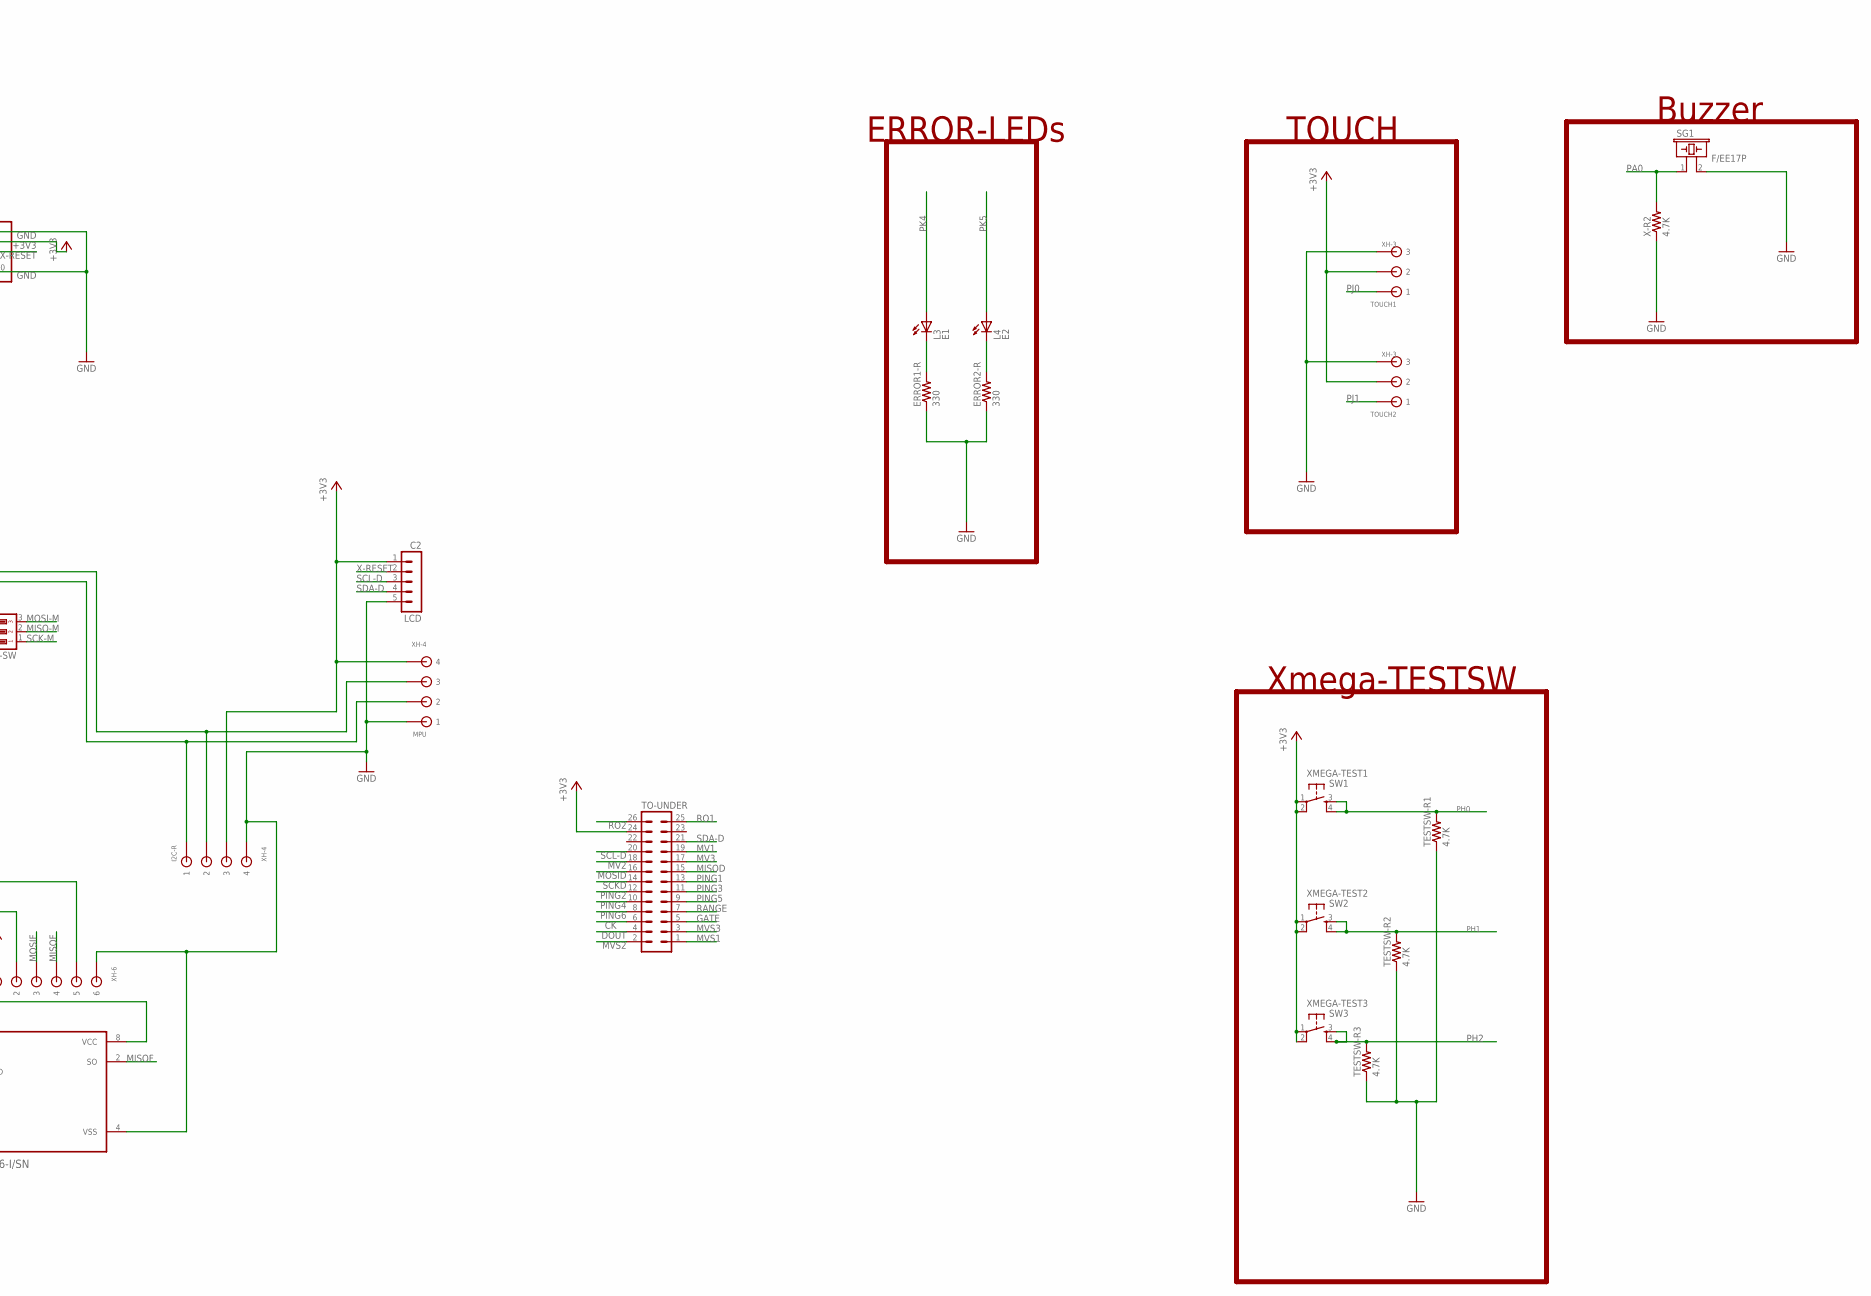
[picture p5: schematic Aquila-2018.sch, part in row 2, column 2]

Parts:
3.3C1, 5C1, 9C1: 100u; E2,5-6
3.3C2, 5C2, 9C2: 0.1u; C0805
3.3REG, 5VREG: OKL-T_6-W12N-C; OKL-T/3-W5
C1, C3: 22uF25V; C2012
C2, C4: 10uF10V; C2012
CHECKLED: OSTA71A1D-A
ERROR1-R, ERROR2-R: 330; R0805
FT232-R8, FT232-R9: 330; R0805
FT232-R10: 4.7K; R0805
FT232-R11: 10K; R0805
FT232-R12: 1K; R0805
FT232-R13, FT232-R14: 23; R0805
FT232USBCON: Wrie-USB; 32005-201
FT-POWERLED: LEDCHIPLED_0805; CHIPLED_0805
GND-CH: SMD5; SMD2,54-5,08
GND-CHK, GND-CHK1: 2,15/1,0
I2C-R: XH-4; CON4
IC1: FT232RL; SSOP28
IC2: ULN2003AN; DIL16
INDILED1, INDILED2, INDILED3, INDILED4: 330; R0805
J1: XH-5; CON5
JTAG: 20021221-00010C4LF
L3: E1; LED5MM
L4: E2; LED5MM
L5: RXDLED; CHIPLED_0805
L6: TXDLED; CHIPLED_0805
LCD: C2; MA05-1
M1-R1, M2-R1: 4.7K; R0805
M-SW: TL36PO; TL3XPO
MAIN-SPL: XH-2; CON2
MAINSW2: MA03-1
MEGA1, MEGA2: MEGA8-AI; TQFP32-08
MEGA1-C1, MEGA2-C1: 0.1u; C0805
MOTORDRIVER: ML14
MPU: XH-4; CON4
Q1, Q2: 20MHz; CSTLS_X
Q3, Q4, Q5: IRF9530; TO220BV
R1, R2: 1.2k; 0204/7
R-B: ?; R0805
R-G: ?; R0805
R-R: ?; R0805
RESET-MEGA1: R-1; DTS-6
RESET-MEGA2: R-2; DTS-6
RESET-XMEGA: DTS-6
S1: DIP08S
S2: M251
SG1: F/EE17P
SL-R1: 1K; R0805
SP-LED: LEDCHIPLED_0805; CHIPLED_0805
SP-R1, SP-R3: 1.2k; R0805
SP-R2, SP-R4: 20K; R0805
SP-R5, SP-R6: 4.7K; R0805
SP-RC1, SP-RC2: 20k; RTRIM3296W
SP-SW2: 219-02; CTS-219-02
SPI-R: XH-6; CON6
SPI-SW: DIP03YL
SRAM-R1: 4.7K; R0805
SRAM-R2: 10k; R0805
SS-R1, SS-R2: 4.7K; R0805
STEPINDI1, STEPINDI2, STEPINDI3: LED; CHIPLED_0805
STEPINDI4: KED; CHIPLED_0805
SUOPPLY-SW2: XH-3; CON3
SUPPLY3.3V, SUPPLY5V, SUPPLY9: MAIN; AK500/2
SV1: ML6
TESTSW-R1, TESTSW-R2, TESTSW-R3: 4.7K; R0805
TO-UNDER: ML26
TOUCH1, TOUCH2: XH-3; CON3
TW-SP: XH-2; CON2
TWILITE: C2; MA05-1
U1: ATXMEGA128A1U-AU; TQFP-100A-100
U2: 23K256-I/SN; SOIC127P600X175-8N
U$2: 5566-04A
VOLTAGE-METER1, VOLTAGE-METER2: XH-2; CON2
X2: DCJACK-MJ179P; MJ-179P
X-R1, X-R2: 4.7K; R0805
XMEGA-C1, XMEGA-C2: 0.1u; C0805
XMEGA-TEST1: SW1; DTS-6
XMEGA-TEST2: SW2; DTS-6
XMEGA-TEST3: SW3; DTS-6

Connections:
+3V3: 3.3C1.+, 3.3C2.1, 3.3REG.4 (VOUT), 3.3REG.5 (SENSE), C4.1, CHECKLED.ANODE, I2C-R.P$3 (3), JTAG.4, LCD.1, M1-R1.2, M2-R1.2, MEGA1.4 (VCC), MEGA1.6 (VCC), MEGA1.18 (AVCC), MEGA1.20 (AREF), MEGA1-C1.1, MEGA2.4 (VCC), MEGA2.6 (VCC), MEGA2.18 (AVCC), MEGA2.20 (AREF), MEGA2-C1.2, MOTORDRIVER.11, MPU.P$4 (4), R2.1, S2.1 (O), SPI-R.P$1 (1), SRAM-R1.2, SRAM-R2.2, SS-R1.2, SS-R2.2, SUPPLY3.3V.1, SV1.2, TO-UNDER.24, TOUCH1.P$2 (2), TOUCH2.P$2 (2), TW-SP.P$2 (2), U1.4 (AVCC), U1.14 (VCC), U1.24 (VCC), U1.34 (VCC), U1.44 (VCC), U1.54 (VCC), U1.64 (VCC), U1.74 (VCC), U1.83 (VCC), U1.94 (AVCC), U2.8 (VCC), U$2.4, X-R1.2, XMEGA-C1.1, XMEGA-C2.1, XMEGA-TEST1.1, XMEGA-TEST1.2, XMEGA-TEST2.1, XMEGA-TEST2.2, XMEGA-TEST3.1, XMEGA-TEST3.2
+5V: 5C1.+, 5C2.1, 5VREG.4 (VOUT), 5VREG.5 (SENSE), C2.1, IC2.9 (CD+), INDILED1.2, INDILED2.2, INDILED3.2, INDILED4.2, J1.P$1 (1), R1.1, S2.3 (S), SP-LED.A, SUPPLY5V.1, U$2.3
+9V: 3.3REG.2 (VIN), 5VREG.2 (VIN), 9C1.+, 9C2.1, C1.1, C3.1, MAIN-SPL.P$1 (1), Q4.S, Q5.D, SP-R2.2, SP-R4.2, SP-R5.2, VOLTAGE-METER1.P$1 (1)
CK: TO-UNDER.6, U1.46 (PF1)
CS: SRAM-R1.1, U1.82 (PK7), U2.1 (~CS)
DOUT: TO-UNDER.4, U1.48 (PF3)
FT232-RXD: IC1.5 (RXD), L5.A, S1.10 (2), S1.12 (2), S1.14 (2), TWILITE.4
FT232-TXD: IC1.1 (TXD), L6.A, S1.9 (2), S1.11 (2), S1.13 (2), TWILITE.2
FT-POWERLED1: FT232-R12.2, FT-POWERLED.C
FT-RESET: IC1.6 (!RI), S1.15 (2), S1.16 (2)
GATE: TO-UNDER.5, U1.47 (PF2)
GND: 3.3C1.-, 3.3C2.2, 3.3REG.3 (GND_1), 3.3REG.7 (GND_2), 5C1.-, 5C2.2, 5VREG.3 (GND_1), 5VREG.7 (GND_2), 9C1.-, 9C2.2, C1.2, C2.2, C3.2, C4.2, ERROR1-R.1, ERROR2-R.1, FT232-R8.1, FT232-R9.1, FT232-R11.1, FT232-R12.1, FT232USBCON.5, FT232USBCON.M1 (S1), FT232USBCON.M2 (S2), FT232USBCON.M3 (S3), FT232USBCON.M4 (S4), GND-CH.1, GND-CHK.1, GND-CHK1.1, I2C-R.P$4 (4), IC1.7 (GND), IC1.18 (GND), IC1.21 (GND), IC1.25 (GND), IC1.26 (TEST), IC2.5 (I5), IC2.6 (I6), IC2.7 (I7), IC2.8 (GND), JTAG.2, JTAG.10, LCD.5, M-SW.3 (S), MAIN-SPL.P$2 (2), MAINSW2.2, MEGA1.3 (GND), MEGA1.5 (GND), MEGA1.21 (GND), MEGA1-C1.2, MEGA2.3 (GND), MEGA2.5 (GND), MEGA2.21 (GND), MEGA2-C1.1, MOTORDRIVER.13, MPU.P$1 (1), Q1.2 (VSS), Q2.2 (VSS), Q3.G, R1.2, R2.2, RESET-MEGA1.3, RESET-MEGA1.4, RESET-MEGA2.3, RESET-MEGA2.4, RESET-XMEGA.3, RESET-XMEGA.4, SG1.2, SL-R1.1, SP-R1.1, SP-R3.1, SP-SW2.3, SP-SW2.4, SPI-R.P$6 (6), SUOPPLY-SW2.P$2 (2), SUPPLY3.3V.2, SUPPLY5V.2, SUPPLY9.2, SV1.6, TESTSW-R1.1, TESTSW-R2.1, TESTSW-R3.1, TOUCH1.P$3 (3), TOUCH2.P$3 (3), TW-SP.P$1 (1), U1.3 (GND), U1.13 (GND), U1.23 (GND), U1.33 (GND), U1.43 (GND), U1.53 (GND), U1.63 (GND), U1.73 (GND), U1.84 (GND), U1.93 (GND), U2.4 (VSS), U$2.2, VOLTAGE-METER1.P$2 (2), VOLTAGE-METER2.P$2 (2), X2.2, X-R2.1, XMEGA-C1.2, XMEGA-C2.2
HOLD: SRAM-R2.1, U2.7 (~HOLD)
M1CS: MEGA1.25 (PC2(ADC2)), MOTORDRIVER.6
M1EN: MEGA1.28 (PC5(ADC5/SCL)), MOTORDRIVER.10
M1INA: MEGA1.27 (PC4(ADC4/SDA)), MOTORDRIVER.9
M1INB: MEGA1.26 (PC3(ADC3)), MOTORDRIVER.8
M1PWM: MEGA1.10 (PD6(AIN0)), MOTORDRIVER.7
M2CS: MEGA2.25 (PC2(ADC2)), MOTORDRIVER.1
M2EN: MEGA2.28 (PC5(ADC5/SCL)), MOTORDRIVER.5
M2INA: MEGA2.27 (PC4(ADC4/SDA)), MOTORDRIVER.4
M2INB: MEGA2.26 (PC3(ADC3)), MOTORDRIVER.3
M2PWM: MEGA2.10 (PD6(AIN0)), MOTORDRIVER.2
MISO-M: IC1.11 (!CTS), MEGA1.16 (PB4(MISO)), MEGA2.16 (PB4(MISO)), SPI-SW.2
MISO-X: SPI-SW.5, U1.21 (PC6)
MISOD: TO-UNDER.15, U1.31 (PD6)
MISOF: SPI-R.P$4 (4), U1.51 (PF6), U2.2 (SO)
MOSI-M: IC1.10 (!DCD), MEGA1.15 (PB3(MOSI/OC2)), MEGA2.15 (PB3(MOSI/OC2)), SPI-SW.3
MOSI-X: SPI-SW.4, U1.20 (PC5)
MOSID: TO-UNDER.16, U1.30 (PD5)
MOSIF: SPI-R.P$3 (3), U1.50 (PF5), U2.5 (SI)
MV1: TO-UNDER.19, U1.27 (PD2)
MV2: TO-UNDER.18, U1.28 (PD3)
MV3: TO-UNDER.17, U1.29 (PD4)
MVS1: TO-UNDER.1, U1.70 (PJ5)
MVS2: TO-UNDER.2, U1.71 (PJ6)
MVS3: TO-UNDER.3, U1.72 (PJ7)
unnamed: IC2.4 (I4), U1.75 (PK0)
unnamed: SP-R1.2, SP-RC1.1 (A), SP-RC1.2 (S)
unnamed: IC2.3 (I3), U1.76 (PK1)
unnamed: Q3.S, Q5.S, SP-R6.2
unnamed: Q4.D, U$2.1
unnamed: SP-R3.2, SP-RC2.1 (A), SP-RC2.2 (S)
unnamed: M-SW.2, Q4.G
unnamed: 5VREG.6 (TRIM), SP-RC1.3 (E)
unnamed: M-SW.1 (O), SP-R5.1
unnamed: S2.2, VOLTAGE-METER2.P$1 (1)
unnamed: IC2.2 (I2), U1.77 (PK2)
unnamed: 3.3REG.6 (TRIM), SP-RC2.3 (E)
unnamed: IC2.1 (I1), U1.78 (PK3)
unnamed: 3.3REG.1 (ON/OFF), SP-R4.1, SP-SW2.2
unnamed: IC2.16 (O1), J1.P$2 (2), STEPINDI1.C
unnamed: IC2.15 (O2), J1.P$3 (3), STEPINDI2.C
unnamed: IC2.14 (O3), J1.P$4 (4), STEPINDI3.C
unnamed: IC2.13 (O4), J1.P$5 (5), STEPINDI4.C
unnamed: INDILED4.1, STEPINDI4.A
unnamed: INDILED3.1, STEPINDI3.A
unnamed: INDILED2.1, STEPINDI2.A
unnamed: INDILED1.1, STEPINDI1.A
unnamed: SL-R1.2, SP-LED.C
unnamed: 5VREG.1 (ON/OFF), SP-R2.1, SP-SW2.1
unnamed: MEGA2.7 (PB6(XTAL1/TOSC1)), Q2.1
unnamed: MEGA2.8 (PB7(XTAL2/TOSC2)), Q2.3
unnamed: MEGA1.7 (PB6(XTAL1/TOSC1)), Q1.1
unnamed: MEGA1.8 (PB7(XTAL2/TOSC2)), Q1.3
unnamed: Q3.D, SUPPLY9.1, X2.1
unnamed: MAINSW2.1, Q5.G, SP-R6.1, SUOPPLY-SW2.P$1 (1)
unnamed: FT232-R9.2, L5.C
unnamed: FT232-R8.2, L6.C
unnamed: FT232-R14.2, FT232USBCON.2
unnamed: FT232-R10.2, FT232USBCON.1, FT-POWERLED.A, IC1.20 (VCC)
unnamed: ERROR1-R.2, L3.K (C)
unnamed: ERROR2-R.2, L4.K (C)
unnamed: FT232-R10.1, FT232-R11.2, IC1.19 (!RESET)
unnamed: FT232-R13.2, FT232USBCON.3
unnamed: FT232-R13.1, IC1.15 (USBDP)
unnamed: FT232-R14.1, IC1.16 (USBDM)
unnamed: IC1.4 (VCCIO), IC1.17 (3V3OUT)
unnamed: CHECKLED.RED, R-R.2
unnamed: CHECKLED.GREEN, R-G.2
unnamed: CHECKLED.BLUE, R-B.2
unnamed: SV1.1, U1.89 (PDI)
PA0: SG1.1, U1.95 (PA0), X-R2.2
PH0: TESTSW-R1.2, U1.55 (PH0), XMEGA-TEST1.3, XMEGA-TEST1.4
PH1: TESTSW-R2.2, U1.56 (PH1), XMEGA-TEST2.3, XMEGA-TEST2.4
PH2: TESTSW-R3.2, U1.57 (PH2), XMEGA-TEST3.3, XMEGA-TEST3.4
PING1: TO-UNDER.13, U1.35 (PE0)
PING2: TO-UNDER.12, U1.36 (PE1)
PING3: TO-UNDER.11, U1.37 (PE2)
PING4: TO-UNDER.10, U1.38 (PE3)
PING5: TO-UNDER.9, U1.39 (PE4)
PING6: TO-UNDER.8, U1.40 (PE5)
PJ0: TOUCH1.P$1 (1), U1.65 (PJ0)
PJ1: TOUCH2.P$1 (1), U1.66 (PJ1)
PK4: L3.A, U1.79 (PK4)
PK5: L4.A, U1.80 (PK5)
PQ0: R-R.1, U1.85 (PQ0)
PQ1: R-G.1, U1.86 (PQ1)
PQ2: R-B.1, U1.87 (PQ2)
RANGE: TO-UNDER.7, U1.45 (PF0)
RESET-M1: M1-R1.1, MEGA1.29 (PC6(/RESET)), RESET-MEGA1.1, RESET-MEGA1.2, S1.1
RESET-M2: M2-R1.1, MEGA2.29 (PC6(/RESET)), RESET-MEGA2.1, RESET-MEGA2.2, S1.2 (1)
RO1: MEGA1.32 (PD2(INT0)), TO-UNDER.25
RO2: MEGA2.32 (PD2(INT0)), TO-UNDER.26
RXDM1: MEGA1.30 (PD0(RXD)), S1.6 (1)
RXDM2: MEGA2.30 (PD0(RXD)), S1.4 (1)
RXDX1: S1.8 (1), U1.17 (PC2)
SCK-M: IC1.9 (!DSR), MEGA1.17 (PB5(SCK)), MEGA2.17 (PB5(SCK)), SPI-SW.1
SCK-X: SPI-SW.6, U1.22 (PC7)
SCKD: TO-UNDER.14, U1.32 (PD7)
SCKF: SPI-R.P$2 (2), U1.52 (PF7), U2.6 (SCK)
SCL-C: I2C-R.P$1 (1), MPU.P$2 (2), U1.16 (PC1)
SCL-D: LCD.3, TO-UNDER.20, U1.26 (PD1)
SDA-C: I2C-R.P$2 (2), MPU.P$3 (3), U1.15 (PC0)
SDA-D: LCD.4, TO-UNDER.21, U1.25 (PD0)
SIG1: MEGA1.1 (PD3(INT1)), U1.5 (PB0)
SIG2: MEGA2.1 (PD3(INT1)), U1.6 (PB1)
SS1: MEGA1.14 (PB2(SS/OC1B)), SS-R1.1, U1.7 (PB2)
SS2: MEGA2.14 (PB2(SS/OC1B)), SS-R2.1, U1.8 (PB3)
SS-R: SPI-R.P$5 (5), U1.49 (PF4)
TCK: JTAG.1, U1.11 (PB6)
TDI: JTAG.9, U1.10 (PB5)
TDO: JTAG.3, U1.12 (PB7)
TMS: JTAG.5, U1.9 (PB4)
TXDM1: MEGA1.31 (PD1(TXD)), S1.5 (1)
TXDM2: MEGA2.31 (PD1(TXD)), S1.3 (1)
TXDX1: S1.7 (1), U1.18 (PC3)
X-RESET: JTAG.6, LCD.2, RESET-XMEGA.1, RESET-XMEGA.2, SV1.5, U1.90 (!RESET!/PDI), X-R1.1

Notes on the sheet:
MOTOR-AREA
SWITCHING-SWITCH
FT232RL
CHECK-LED
Xmega-TESTSW
TOUCH
Buzzer
ERROR-LEDs
電源ピン (予備電源含)

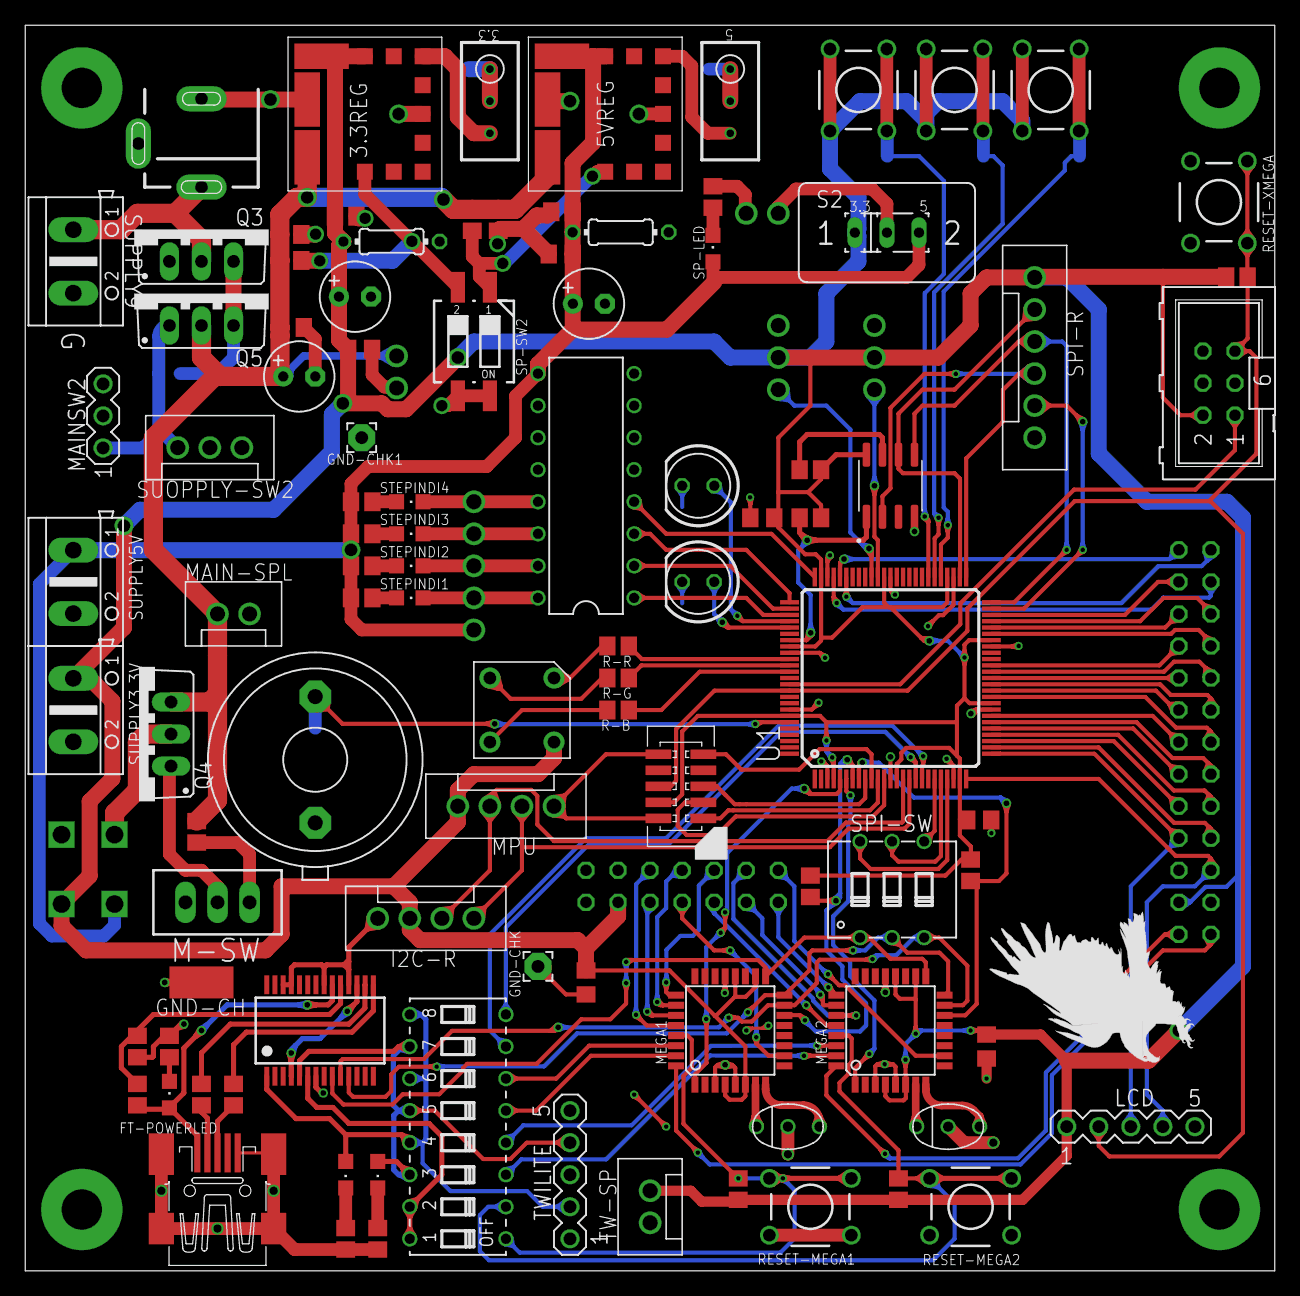
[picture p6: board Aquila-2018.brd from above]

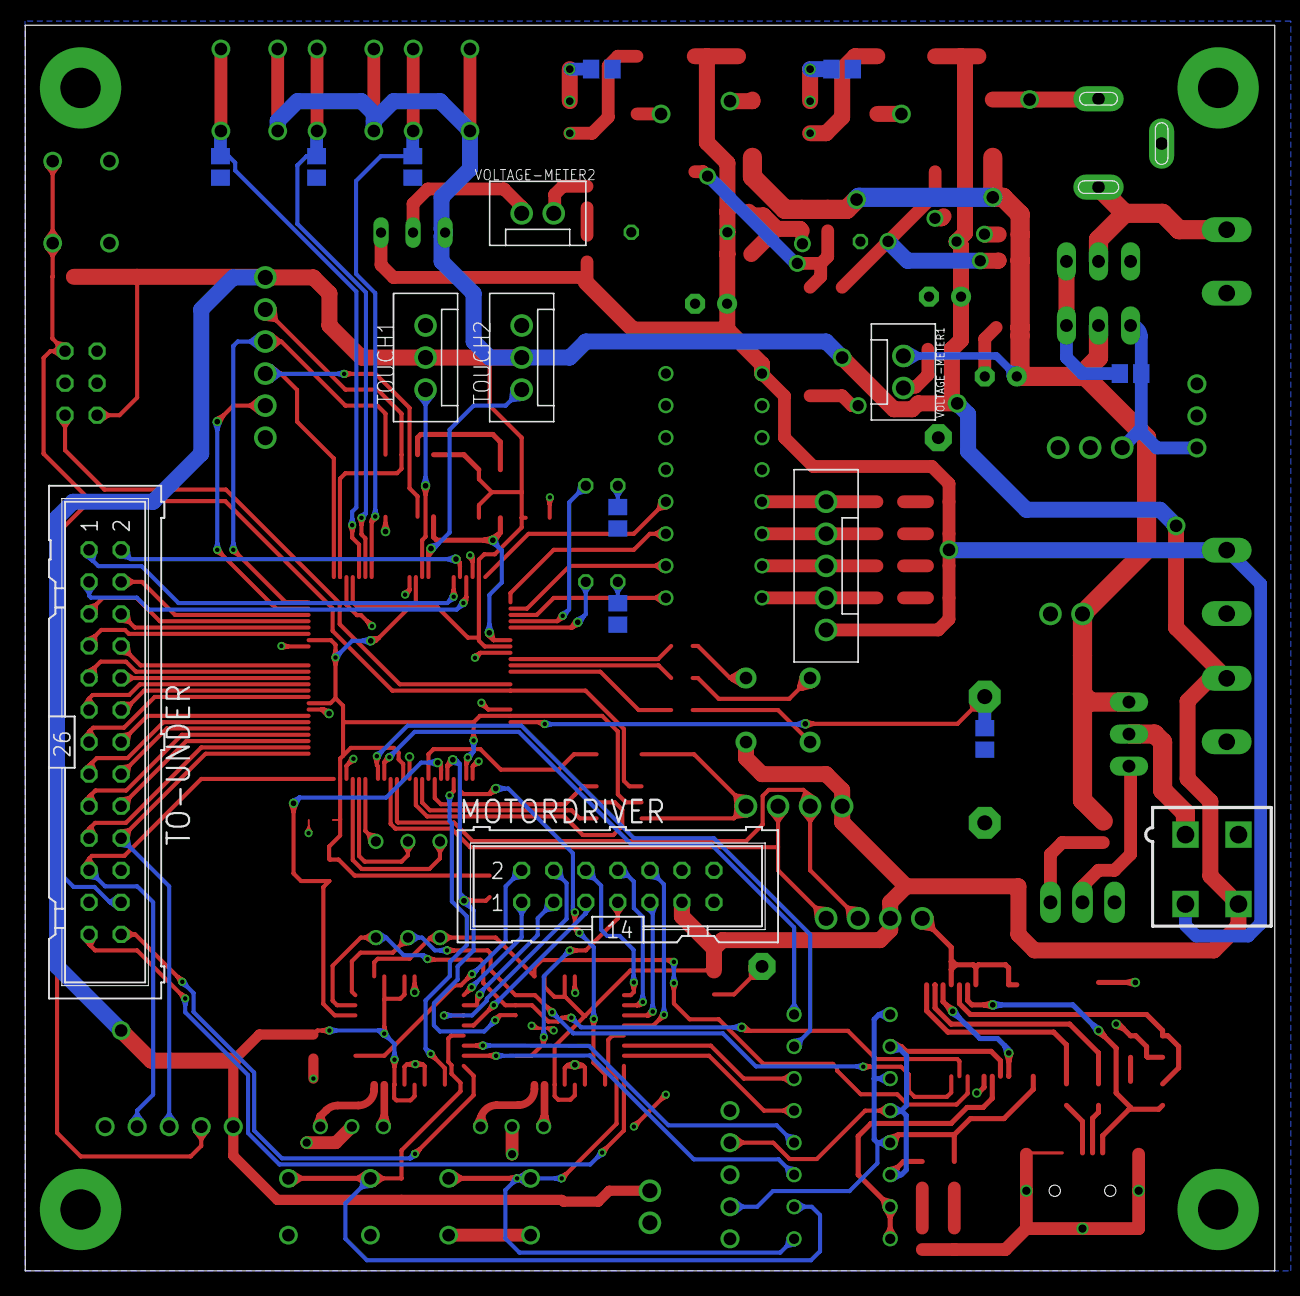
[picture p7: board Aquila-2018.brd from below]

Board: 2 copper layers, 99.0 x 98.7 mm, 116 parts (17 on the bottom side), 128 nets.

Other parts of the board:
U$1: EAGLE-PLC-12MM

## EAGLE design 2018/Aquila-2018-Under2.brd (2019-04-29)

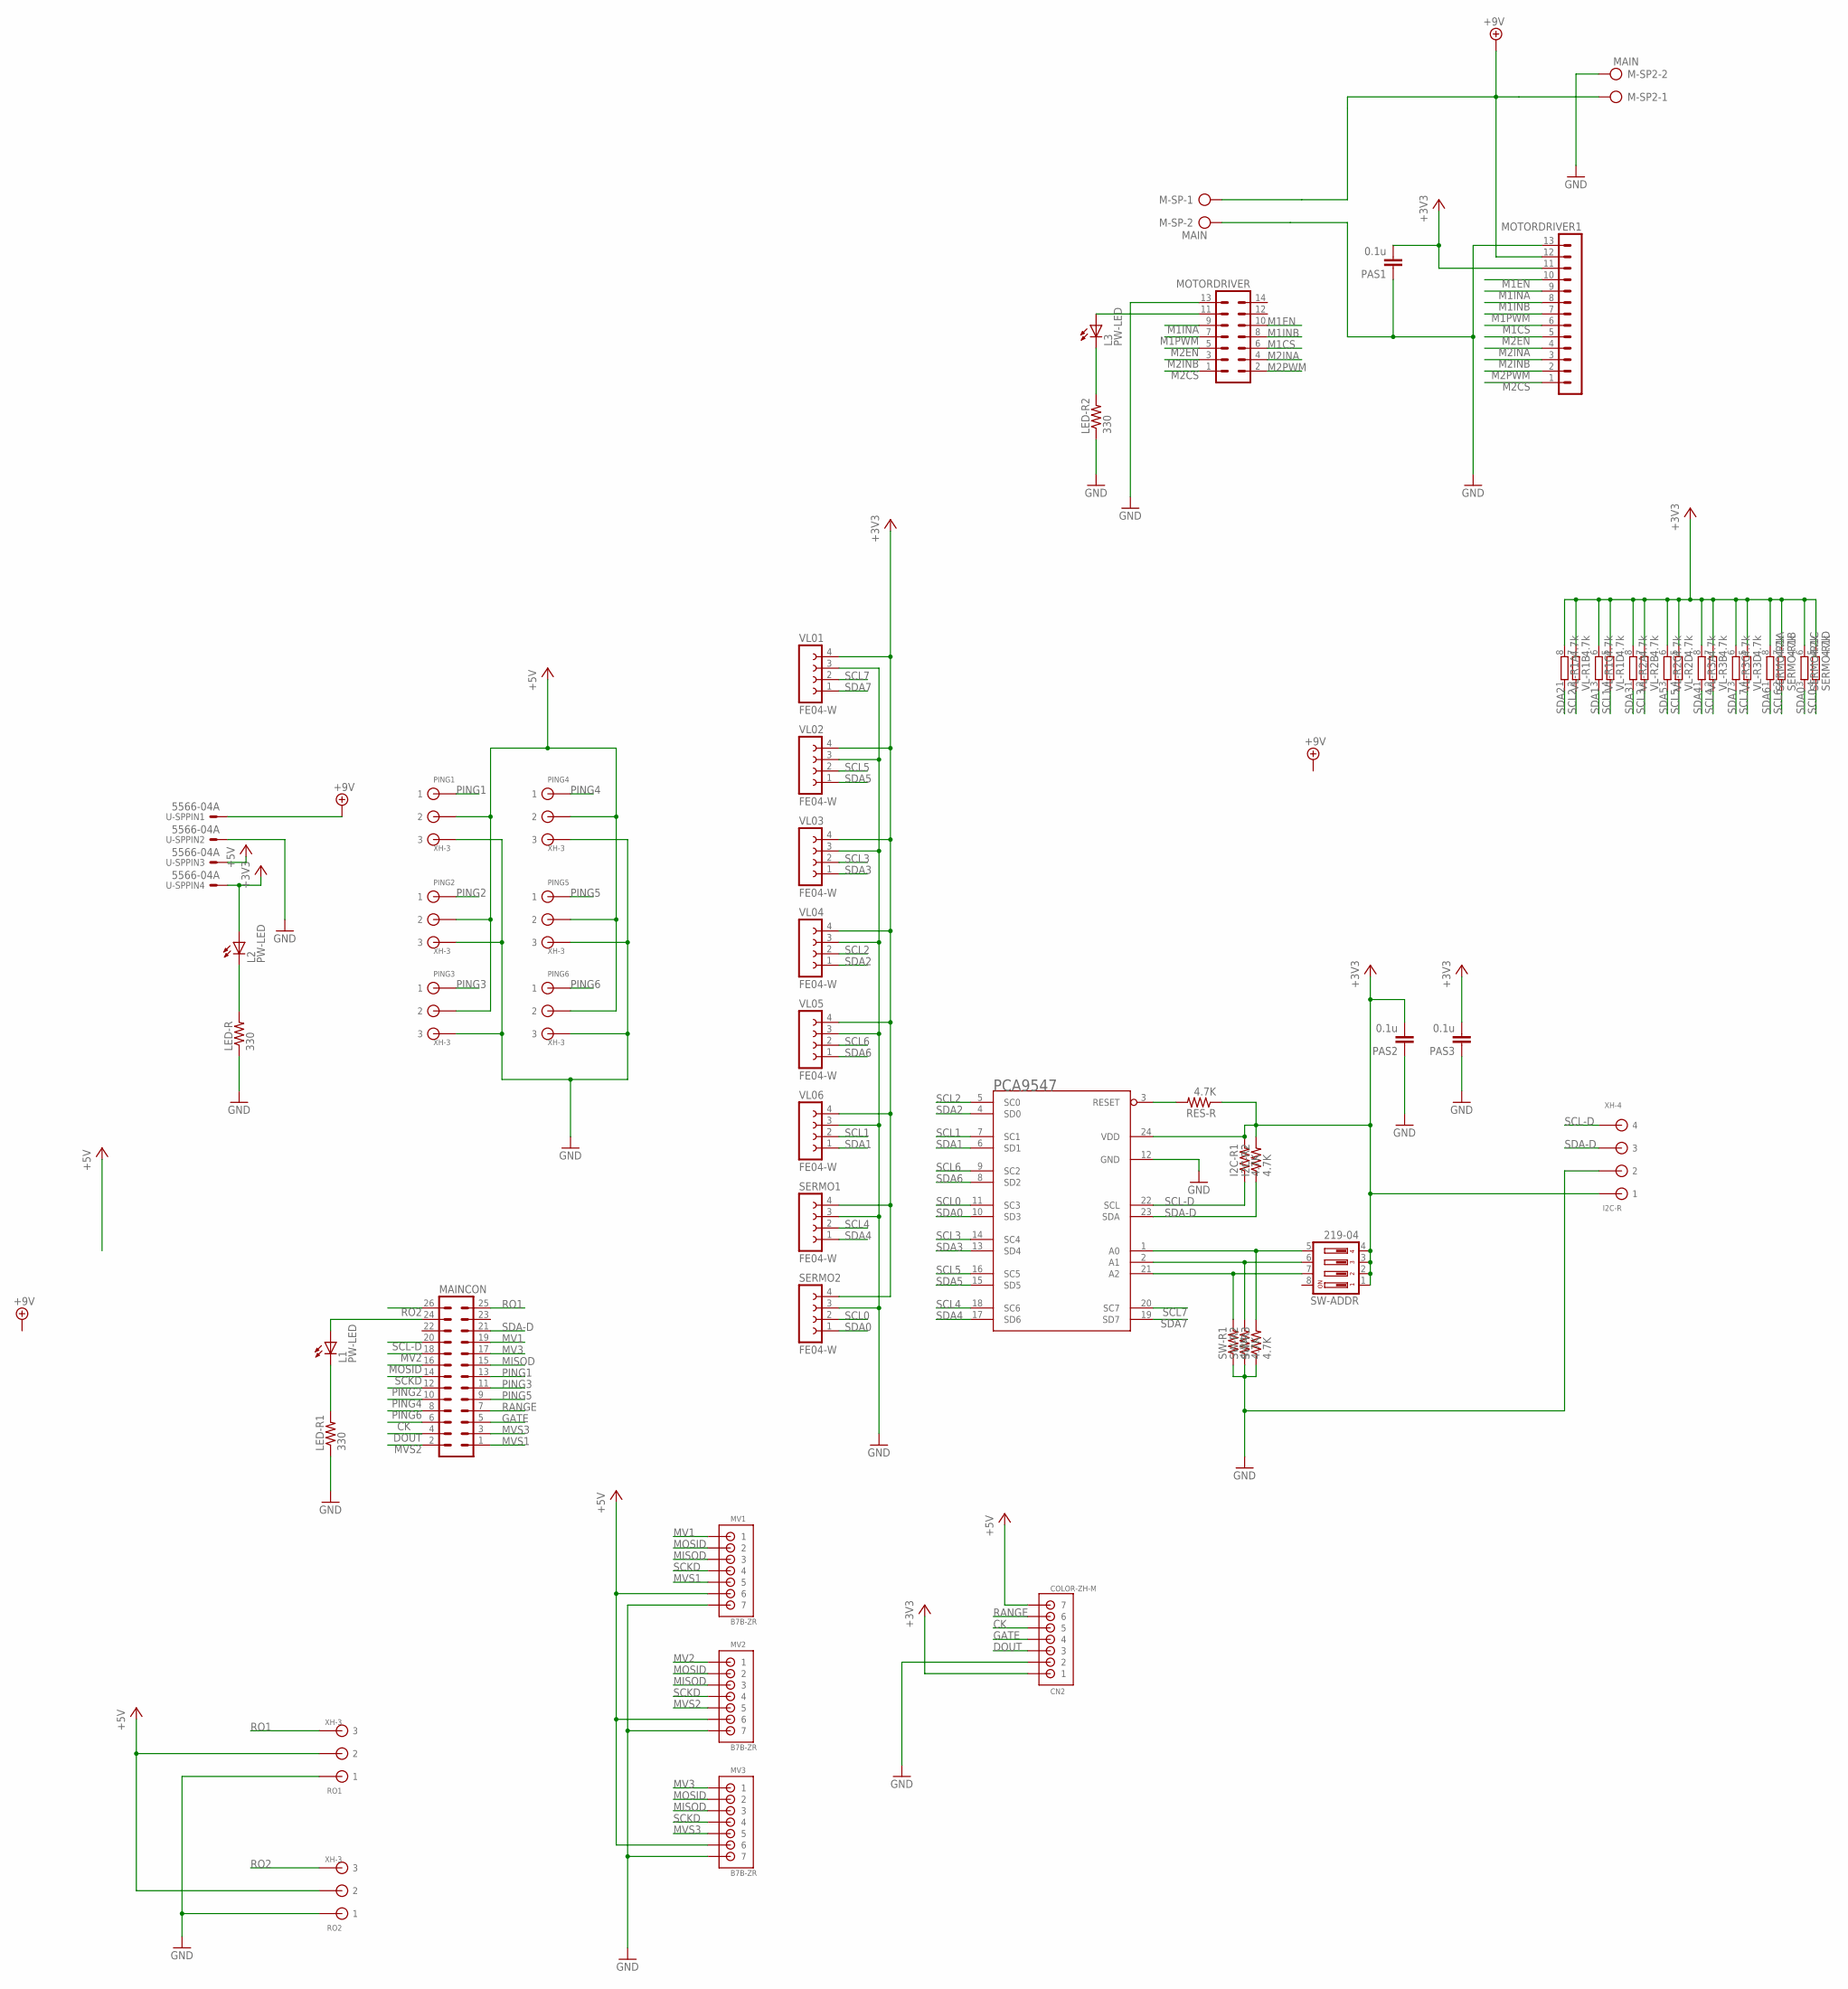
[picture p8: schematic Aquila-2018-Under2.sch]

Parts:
CN2: COLOR-ZH-M; B7B-ZR
I2C-R: XH-4; CON4
I2C-R1, I2C-R2: 4.7K; R0805
L1, L2, L3: PW-LED; CHIPLED_0805
LED-R, LED-R1, LED-R2: 330; R0805
M-SP, M-SP2: MAIN; AK500/2
MAINCON: ML26
MOTORDRIVER: ML14
MOTORDRIVER1: MA13-1
MV1, MV2, MV3: B7B-ZR
PAS1, PAS2, PAS3: 0.1u; C0805
PCA9547: PCA9547; SO24L
PING1, PING2, PING3, PING4, PING5, PING6: XH-3; CON3
RES-R: 4.7K; R0805
RO1, RO2: XH-3; CON3
SERMO1, SERMO2: FE04-W
SERMO-R1: 4.7k; EXB28V
SW-ADDR: 219-04; CTS-219-04
SW-R1, SW-R2, SW-R3: 4.7K; R0805
U-SP: 5566-04A
VL01, VL02, VL03, VL04, VL05, VL06: FE04-W
VL-R1, VL-R2, VL-R3: 4.7k; EXB28V

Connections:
+3V3: CN2.1, I2C-R.P$1 (1), I2C-R1.2, I2C-R2.2, L2.A, MOTORDRIVER1.11, PAS1.2, PAS2.2, PAS3.2, PCA9547.24 (VDD), RES-R.1, SERMO1.4, SERMO2.4, SERMO-R1.5 (2), SERMO-R1.6 (2), SERMO-R1.7 (2), SERMO-R1.8 (2), SW-ADDR.1, SW-ADDR.2, SW-ADDR.3, SW-ADDR.4, U-SP.4, VL01.4, VL02.4, VL03.4, VL04.4, VL05.4, VL06.4, VL-R1.5 (2), VL-R1.6 (2), VL-R1.7 (2), VL-R1.8 (2), VL-R2.5 (2), VL-R2.6 (2), VL-R2.7 (2), VL-R2.8 (2), VL-R3.5 (2), VL-R3.6 (2), VL-R3.7 (2), VL-R3.8 (2)
+5V: CN2.7, MV1.6, MV2.6, MV3.6, PING1.P$2 (2), PING2.P$2 (2), PING3.P$2 (2), PING4.P$2 (2), PING5.P$2 (2), PING6.P$2 (2), RO1.P$2 (2), RO2.P$2 (2), U-SP.3
+9V: M-SP.1, M-SP2.1, MOTORDRIVER1.12, U-SP.1
CK: CN2.5, MAINCON.6
DOUT: CN2.3, MAINCON.4
GATE: CN2.4, MAINCON.5
GND: CN2.2, I2C-R.P$2 (2), LED-R.1, LED-R1.1, LED-R2.1, M-SP.2, M-SP2.2, MOTORDRIVER.13, MOTORDRIVER1.13, MV1.7, MV2.7, MV3.7, PAS1.1, PAS2.1, PAS3.1, PCA9547.12 (GND), PING1.P$3 (3), PING2.P$3 (3), PING3.P$3 (3), PING4.P$3 (3), PING5.P$3 (3), PING6.P$3 (3), RO1.P$1 (1), RO2.P$1 (1), SERMO1.3, SERMO2.3, SW-R1.1, SW-R2.1, SW-R3.1, U-SP.2, VL01.3, VL02.3, VL03.3, VL04.3, VL05.3, VL06.3
M1CS: MOTORDRIVER.6, MOTORDRIVER1.6
M1EN: MOTORDRIVER.10, MOTORDRIVER1.10
M1INA: MOTORDRIVER.9, MOTORDRIVER1.9
M1INB: MOTORDRIVER.8, MOTORDRIVER1.8
M1PWM: MOTORDRIVER.7, MOTORDRIVER1.7
M2CS: MOTORDRIVER.1, MOTORDRIVER1.1
M2EN: MOTORDRIVER.5, MOTORDRIVER1.5
M2INA: MOTORDRIVER.4, MOTORDRIVER1.4
M2INB: MOTORDRIVER.3, MOTORDRIVER1.3
M2PWM: MOTORDRIVER.2, MOTORDRIVER1.2
MISOD: MAINCON.15, MV1.3, MV2.3, MV3.3
MOSID: MAINCON.16, MV1.2, MV2.2, MV3.2
MV1: MAINCON.19, MV1.1
MV2: MAINCON.18, MV2.1
MV3: MAINCON.17, MV3.1
MVS1: MAINCON.1, MV1.5
MVS2: MAINCON.2, MV2.5
MVS3: MAINCON.3, MV3.5
unnamed: PCA9547.1 (A0), SW-ADDR.5, SW-R3.2
unnamed: PCA9547.2 (A1), SW-ADDR.6, SW-R2.2
unnamed: PCA9547.21 (A2), SW-ADDR.7, SW-R1.2
unnamed: L2.C, LED-R.2
unnamed: PCA9547.3 (RESET), RES-R.2
unnamed: L1.C, LED-R1.2
unnamed: L1.A, MAINCON.24
unnamed: L3.C, LED-R2.2
unnamed: L3.A, MOTORDRIVER.11
PING1: MAINCON.13, PING1.P$1 (1)
PING2: MAINCON.12, PING2.P$1 (1)
PING3: MAINCON.11, PING3.P$1 (1)
PING4: MAINCON.10, PING4.P$1 (1)
PING5: MAINCON.9, PING5.P$1 (1)
PING6: MAINCON.8, PING6.P$1 (1)
RANGE: CN2.6, MAINCON.7
RO1: MAINCON.25, RO1.P$3 (3)
RO2: MAINCON.26, RO2.P$3 (3)
SCKD: MAINCON.14, MV1.4, MV2.4, MV3.4
SCL0: PCA9547.11 (SC3), SERMO2.2, SERMO-R1.4 (1)
SCL1: PCA9547.7 (SC1), VL06.2, VL-R1.4 (1)
SCL2: PCA9547.5 (SC0), VL04.2, VL-R1.2 (1)
SCL3: PCA9547.14 (SC4), VL03.2, VL-R2.2 (1)
SCL4: PCA9547.18 (SC6), SERMO1.2, VL-R3.2 (1)
SCL5: PCA9547.16 (SC5), VL02.2, VL-R2.4 (1)
SCL6: PCA9547.9 (SC2), SERMO-R1.2 (1), VL05.2
SCL7: PCA9547.20 (SC7), VL01.2, VL-R3.4 (1)
SCL-D: I2C-R.P$4 (4), I2C-R1.1, MAINCON.20, PCA9547.22 (SCL)
SDA0: PCA9547.10 (SD3), SERMO2.1, SERMO-R1.3 (1)
SDA1: PCA9547.6 (SD1), VL06.1, VL-R1.3 (1)
SDA2: PCA9547.4 (SD0), VL04.1, VL-R1.1
SDA3: PCA9547.13 (SD4), VL03.1, VL-R2.1
SDA4: PCA9547.17 (SD6), SERMO1.1, VL-R3.1
SDA5: PCA9547.15 (SD5), VL02.1, VL-R2.3 (1)
SDA6: PCA9547.8 (SD2), SERMO-R1.1, VL05.1
SDA7: PCA9547.19 (SD7), VL01.1, VL-R3.3 (1)
SDA-D: I2C-R.P$3 (3), I2C-R2.1, MAINCON.21, PCA9547.23 (SDA)

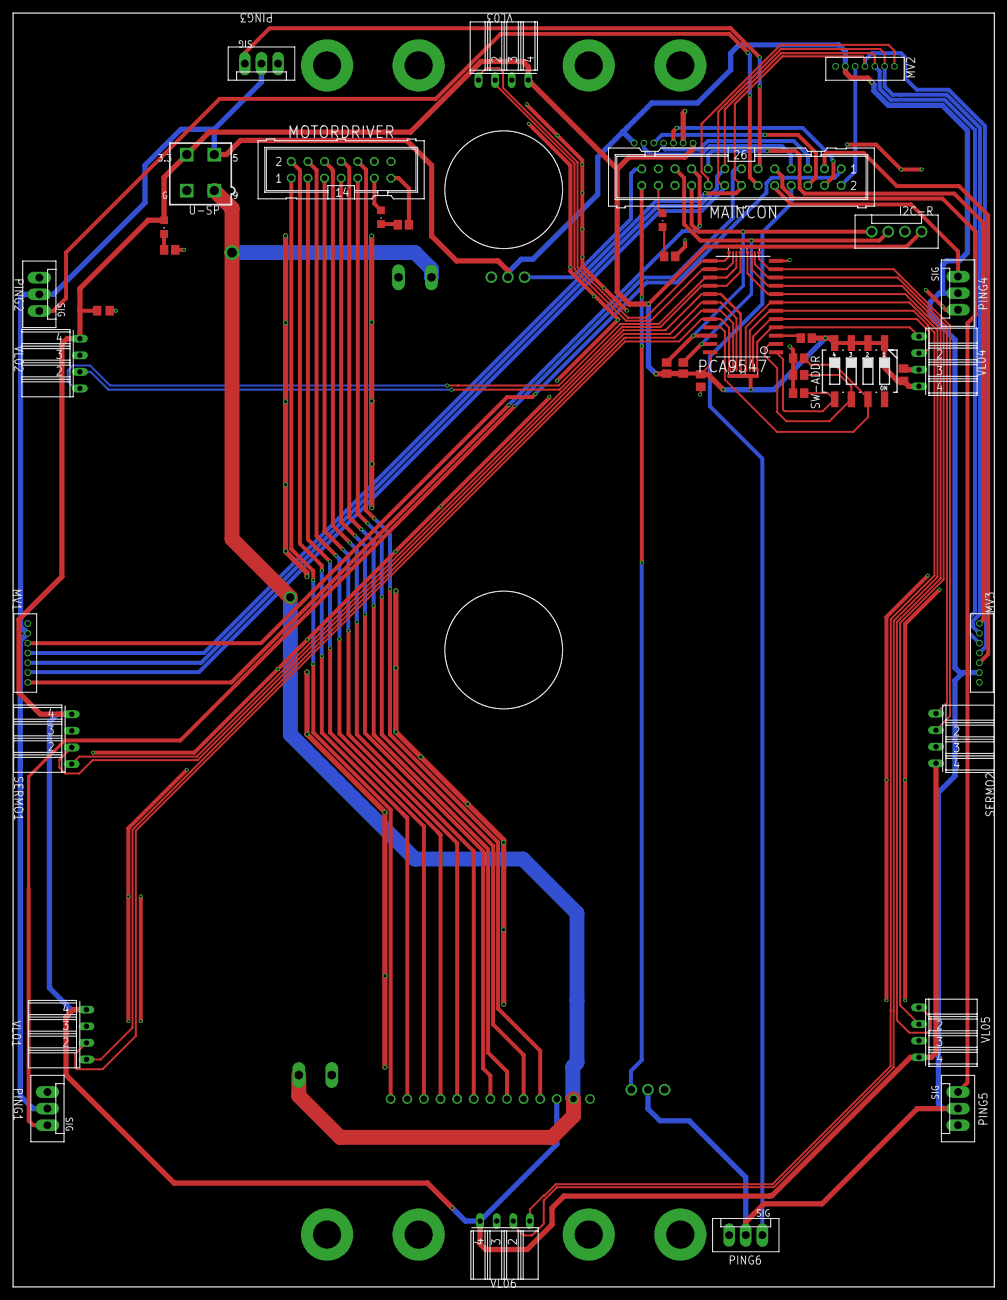
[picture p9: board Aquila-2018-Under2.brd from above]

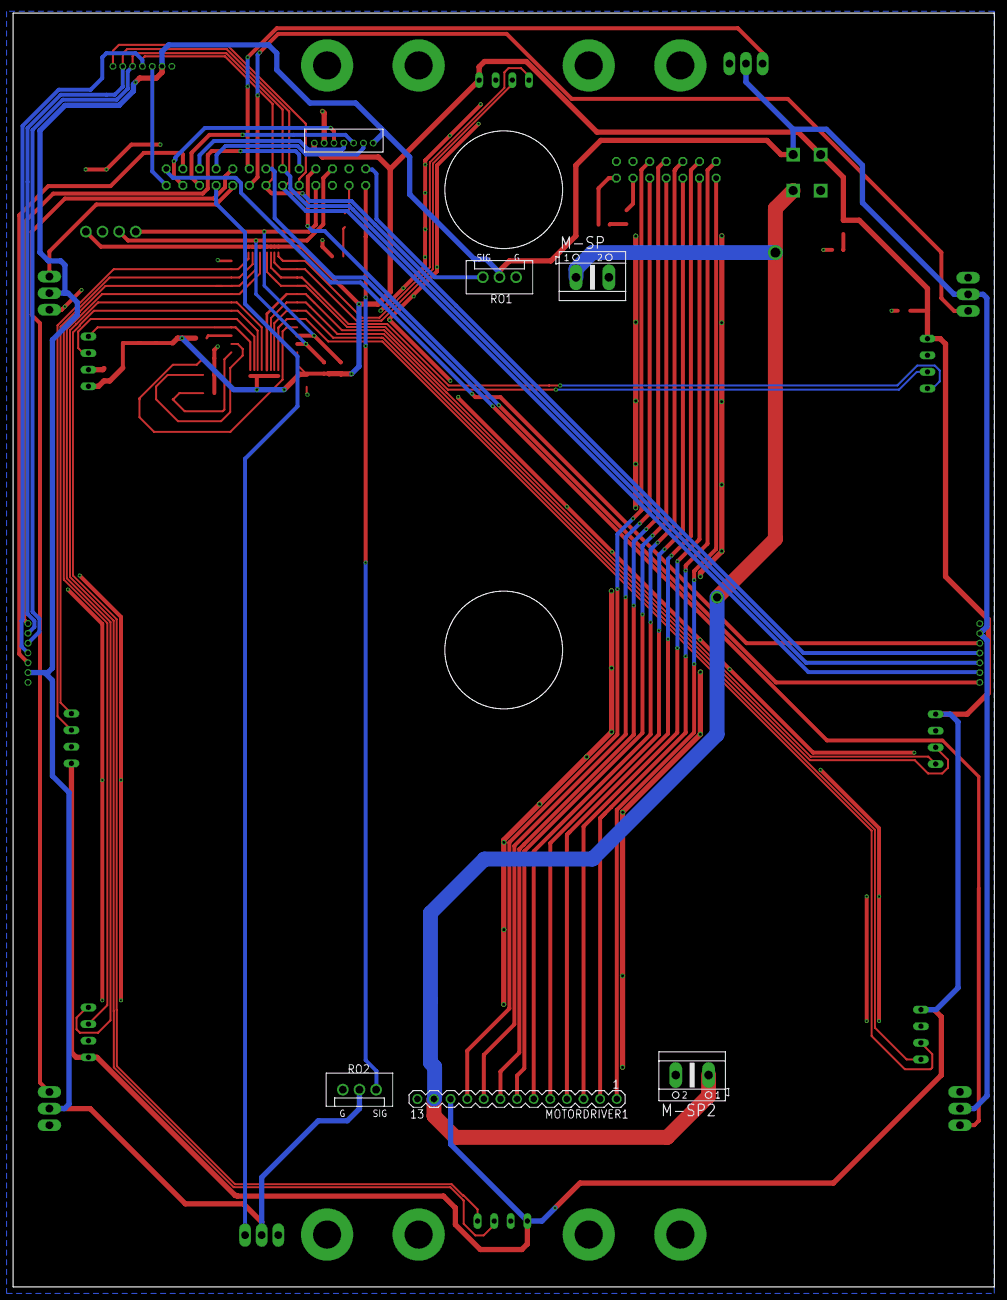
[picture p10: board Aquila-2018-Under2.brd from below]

Board: 2 copper layers, 150.0 x 194.7 mm, 48 parts (6 on the bottom side), 62 nets.

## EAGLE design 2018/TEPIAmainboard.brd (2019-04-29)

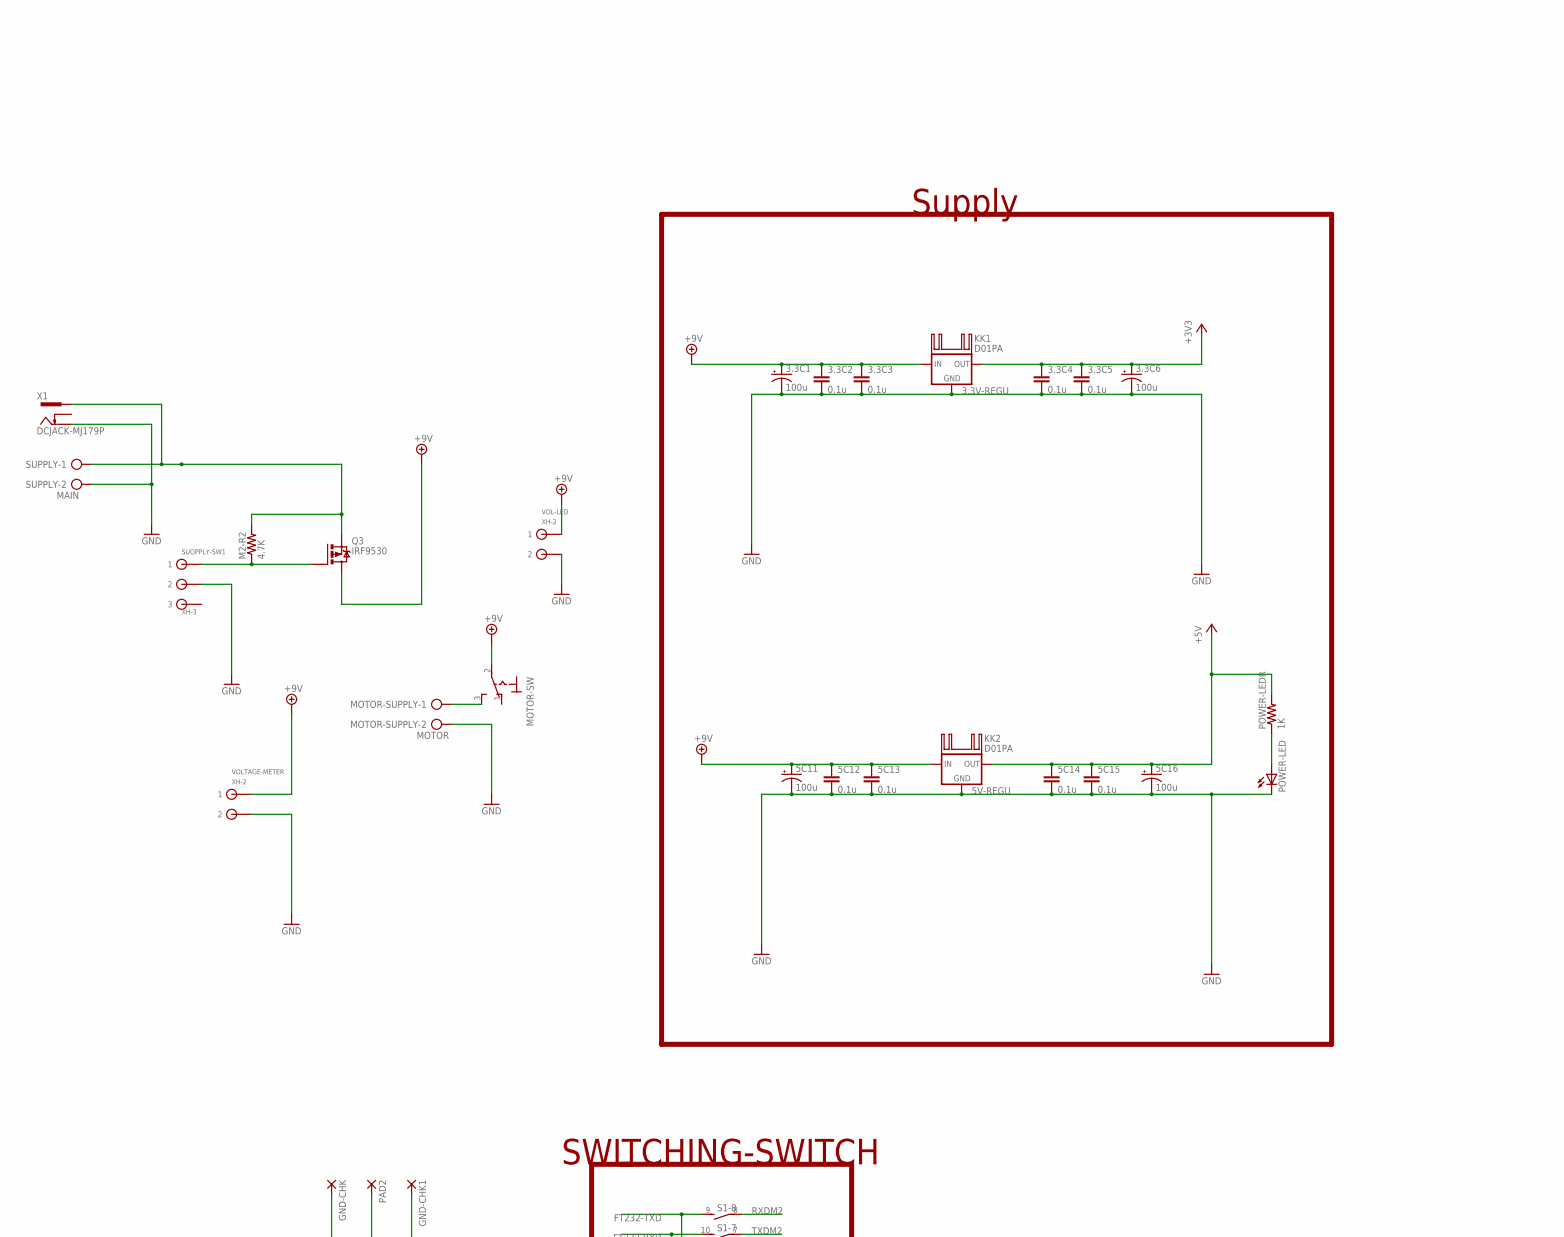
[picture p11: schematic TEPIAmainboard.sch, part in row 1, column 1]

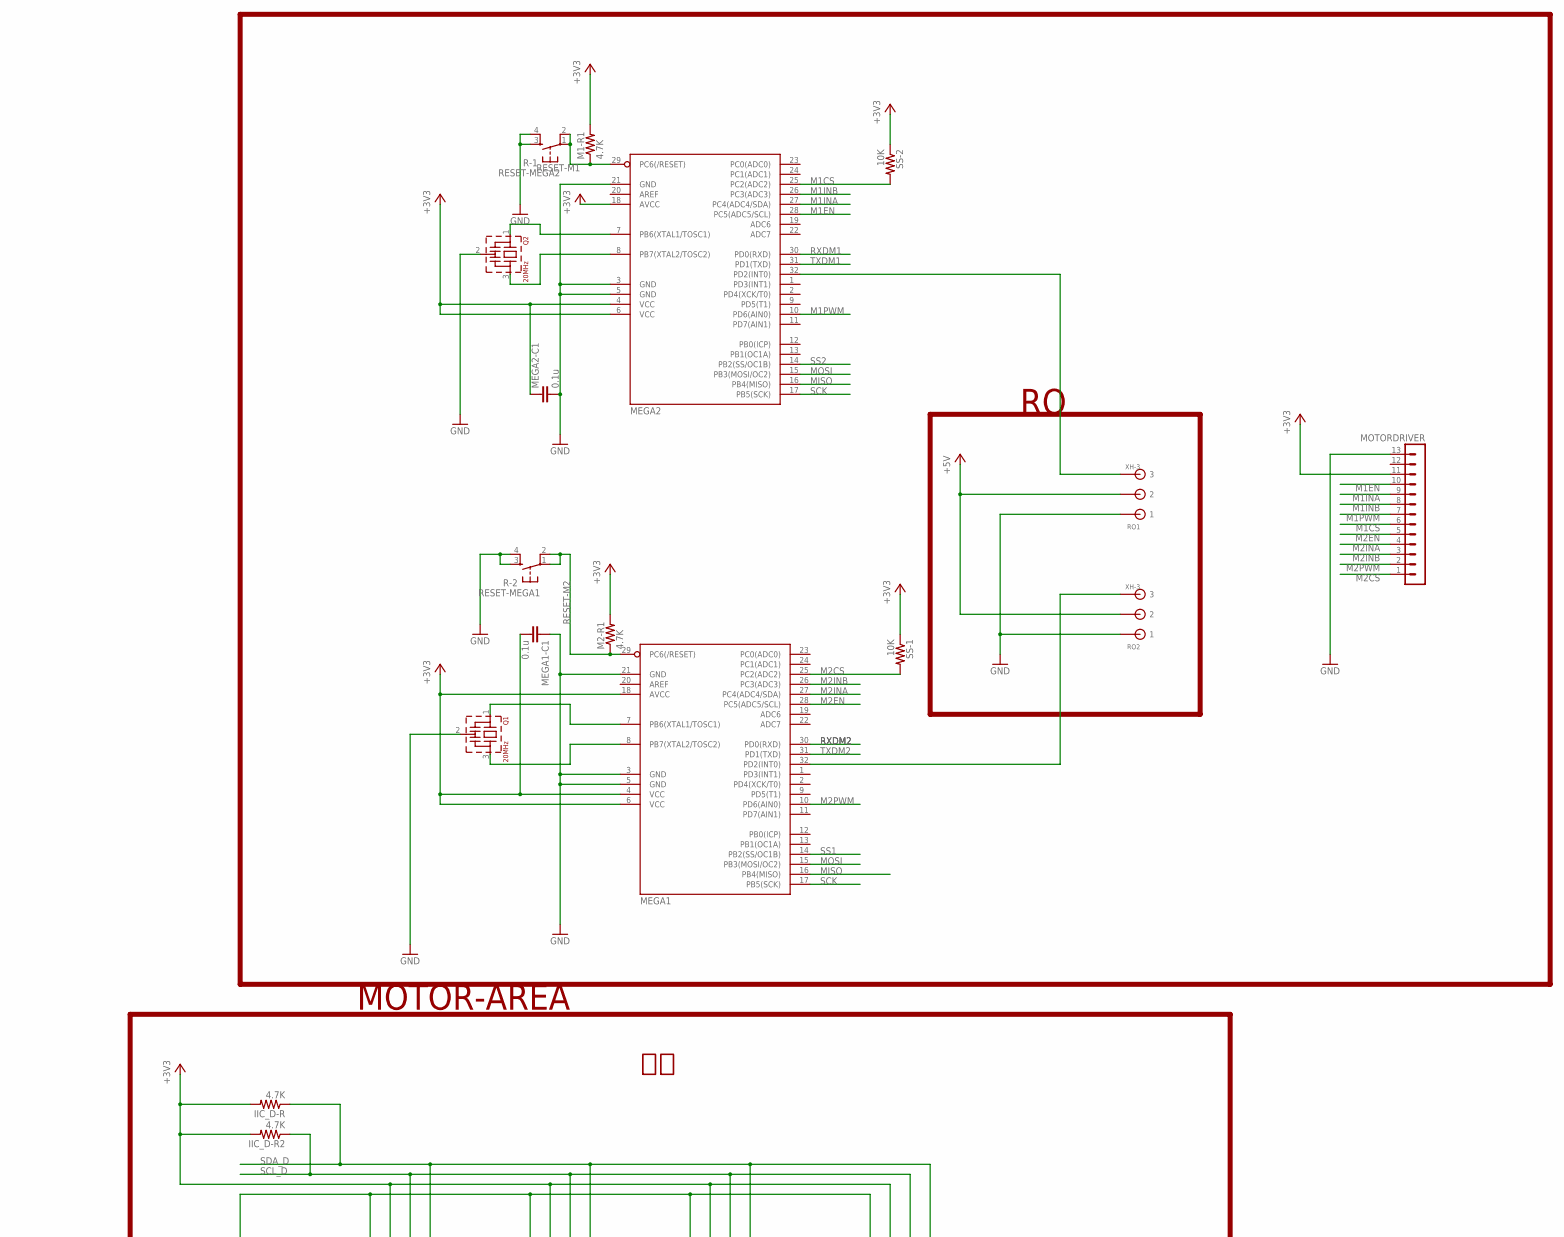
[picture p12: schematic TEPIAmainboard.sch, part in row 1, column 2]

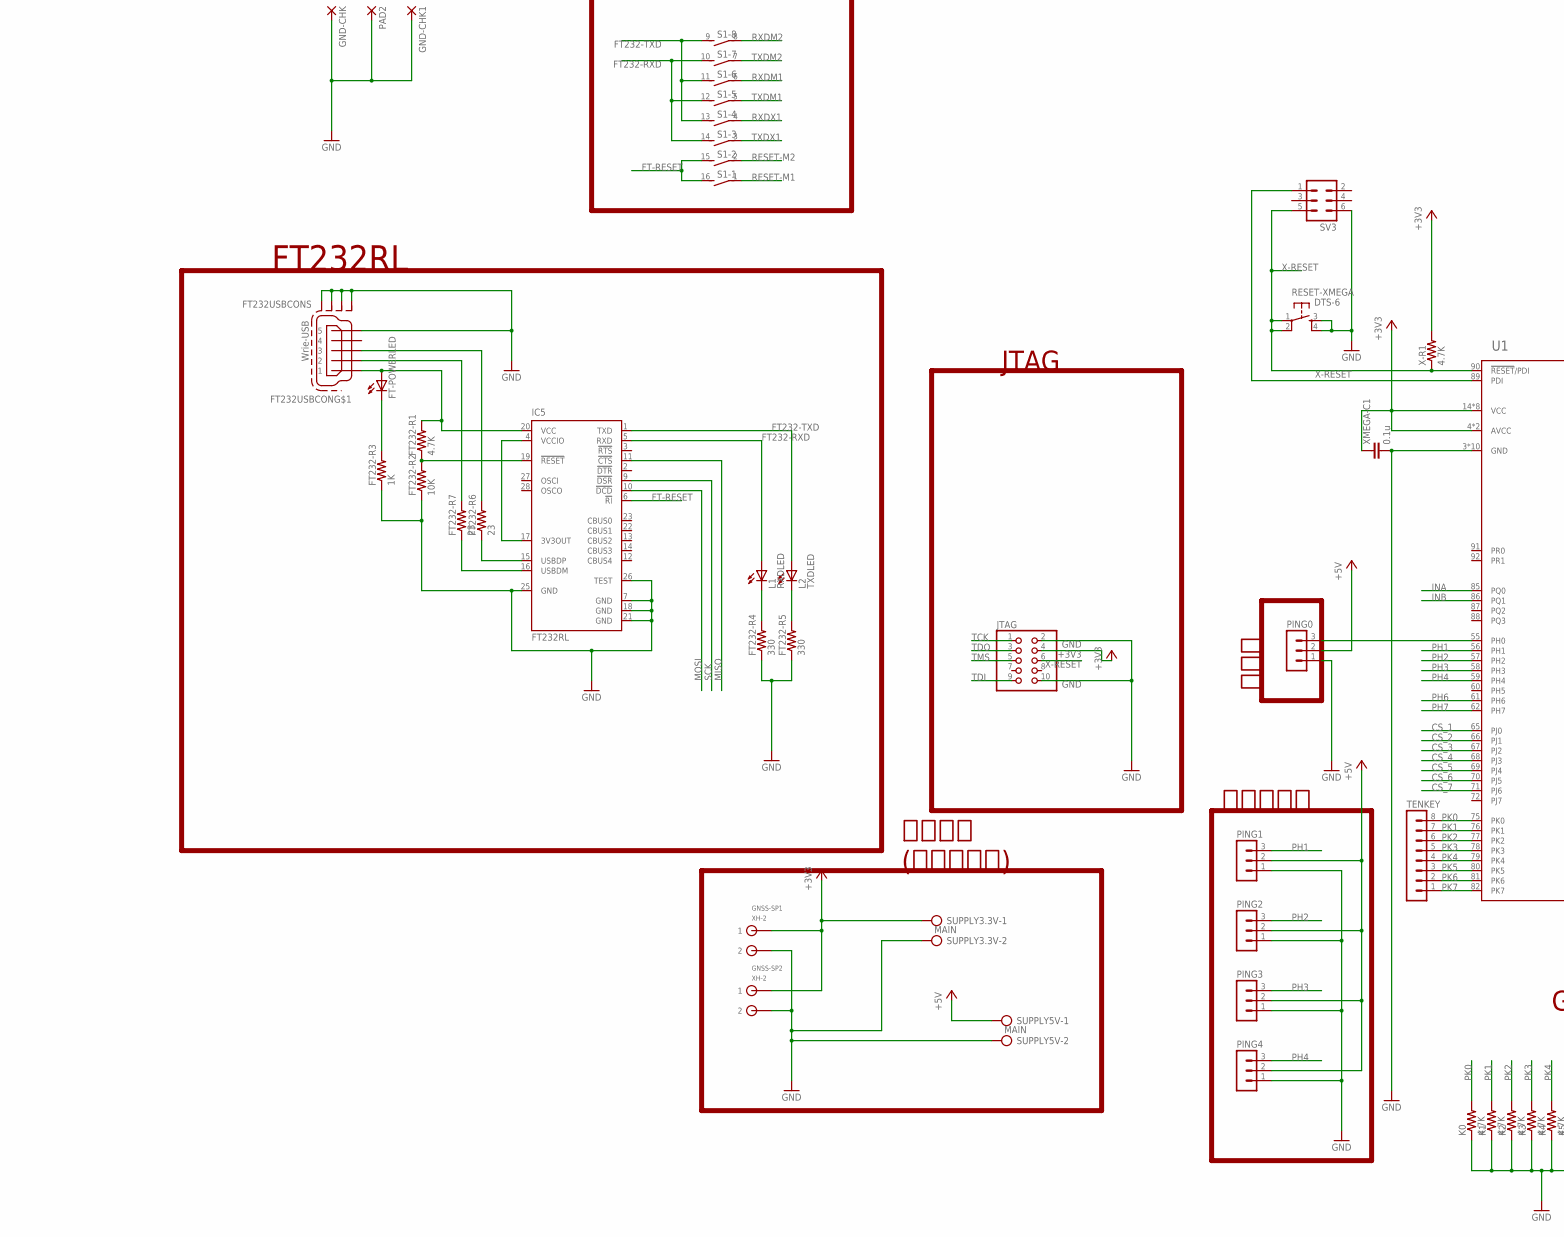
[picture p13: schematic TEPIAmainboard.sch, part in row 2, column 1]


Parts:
3.3C1, 3.3C6, 5C11, 5C16: 100u; E2,5-6
3.3C2, 3.3C3, 3.3C4, 3.3C5, 5C12, 5C13, 5C14, 5C15: 0.1u; C0805
3.3V-REGU, 5V-REGU: 78XXS
FALLING: MA04-1
FT232-R1: 4.7K; R0805
FT232-R2: 10K; R0805
FT232-R3: 1K; R0805
FT232-R4, FT232-R5: 330; R0805
FT232-R6, FT232-R7: 23; R0805
FT232USBCON: Wrie-USB; 32005-201
FT-POWERLED: LEDCHIPLED_0805; CHIPLED_0805
GND-CHK, GND-CHK1: 2,15/1,0
GNSS-SP1, GNSS-SP2: XH-2; CON2
GNSSSPI: MA04-1
GNSSUART: PINHD-1X2; 1X02
IC5: FT232RL; SSOP28
IIC1, IIC2, IIC3, IIC4: XH-4; CON4
IIC-UP1, IIC-UP2: 1K; R0805
IIC_D-R, IIC_D-R2: 4.7K; R0805
INTUART: MA03-1
JTAG: 20021221-00010C4LF
K, K0, K1, K2, K3, K4, K5, K6: 4.7K; R0805
KK1, KK2: D01PA
L1: RXDLED; CHIPLED_0805
L2: TXDLED; CHIPLED_0805
L6: TESTLED; CHIPLED_0805
L6480: MA05-2
LCD: MA09-1
LCD-I2C: LCD-I2C; MA05-1
M1-R1, M2-R1, M2-R2: 4.7K; R0805
MEGA1, MEGA2: MEGA8-AI; TQFP32-08
MEGA1-C1, MEGA2-C1: 0.1u; C0805
MOTOR-SUPPLY: MOTOR; AK500/2
MOTOR-SW: 320-916
MOTORDRIVER: MA13-1
MPU9250: MA10-1
PAD2: SMD5; SMD2,54-5,08
PING0, PING1, PING2, PING3, PING4: MA03-1
POWER-LED: LEDCHIPLED_0805; CHIPLED_0805
POWER-LEDR: 1K; R0805
Q1, Q2: 20MHz; CSTLS_X
Q3: IRF9530; TO220BV
RESET-MEGA1: R-2; DTS-6
RESET-MEGA2: R-1; DTS-6
RESET-XMEGA: DTS-6
RO1, RO2: XH-3; CON3
S1: DIP08S
SPI4, SPI5, SPI6, SPI7: MA05-1
SPI-SW1: DIP03YL
SS-1, SS-2, SS-3: 10K; R0805
SUOPPLY-SW1: XH-3; CON3
SUPPLY, SUPPLY3.3V, SUPPLY5V: MAIN; AK500/2
SV3: ML6
SW6, SW7: XH-2; CON2
SW6-R, SW7-R: 4.7K; R0805
TENKEY: MA08-1
TEST-R: 330; R0805
U1: ATXMEGA128A1U-AU; TQFP-100A-100
VOL-LED: XH-2; CON2
VOLTAGE-METER: XH-2; CON2
X1: DCJACK-MJ179P; MJ-179P
X-R1: 4.7K; R0805
XMEGA-C1: 0.1u; C0805

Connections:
+3V3: 3.3C4.1, 3.3C5.1, 3.3C6.+, 3.3V-REGU.OUT, GNSS-SP1.P$1 (1), GNSS-SP2.P$1 (1), IIC1.P$2 (2), IIC2.P$2 (2), IIC3.P$2 (2), IIC4.P$2 (2), IIC-UP1.1, IIC-UP2.1, IIC_D-R.2, IIC_D-R2.2, JTAG.4, L6480.4, LCD.9, LCD-I2C.1, M1-R1.2, M2-R1.2, MEGA1.4 (VCC), MEGA1.6 (VCC), MEGA1.18 (AVCC), MEGA1-C1.2, MEGA2.4 (VCC), MEGA2.6 (VCC), MEGA2.18 (AVCC), MEGA2-C1.1, MOTORDRIVER.11, MPU9250.1, MPU9250.2, SS-1.1, SS-2.1, SS-3.2, SUPPLY3.3V.1, SW6.P$1 (1), SW7.P$1 (1), U1.4 (AVCC), U1.14 (VCC), U1.24 (VCC), U1.34 (VCC), U1.44 (VCC), U1.54 (VCC), U1.64 (VCC), U1.74 (VCC), U1.83 (VCC), U1.94 (AVCC), X-R1.2, XMEGA-C1.1
+5V: 5C14.1, 5C15.1, 5C16.+, 5V-REGU.OUT, PING0.2, PING1.2, PING2.2, PING3.2, PING4.2, POWER-LEDR.2, RO1.P$2 (2), RO2.P$2 (2), SUPPLY5V.1
+9V: 3.3C1.+, 3.3C2.1, 3.3C3.1, 3.3V-REGU.IN, 5C11.+, 5C12.1, 5C13.1, 5V-REGU.IN, MOTOR-SW.2, Q3.D, VOL-LED.P$1 (1), VOLTAGE-METER.P$1 (1)
CS_1: MPU9250.6, U1.65 (PJ0)
CS_2: L6480.7, U1.66 (PJ1)
CS_3: GNSSSPI.1, U1.67 (PJ2)
CS_4: SPI4.4, U1.68 (PJ3)
CS_5: SPI5.4, U1.69 (PJ4)
CS_6: SPI6.4, U1.70 (PJ5)
CS_7: SPI7.4, U1.71 (PJ6)
D_/RST: LCD.6, U1.48 (PF3)
D_RS: LCD.5
FT232-RXD: IC5.5 (RXD), L1.A, S1.10 (2), S1.12 (2), S1.14 (2)
FT232-TXD: IC5.1 (TXD), L2.A, S1.9 (2), S1.11 (2), S1.13 (2)
FT-POWERLED: FT232-R3.2, FT-POWERLED.C
FT-RESET: IC5.6 (!RI), S1.15 (2), S1.16 (2)
GND: 3.3C1.-, 3.3C2.2, 3.3C3.2, 3.3C4.2, 3.3C5.2, 3.3C6.-, 3.3V-REGU.GND, 5C11.-, 5C12.2, 5C13.2, 5C14.2, 5C15.2, 5C16.-, 5V-REGU.GND, FALLING.4, FT232-R2.1, FT232-R3.1, FT232-R4.1, FT232-R5.1, FT232USBCON.5, FT232USBCON.M1 (S1), FT232USBCON.M2 (S2), FT232USBCON.M3 (S3), FT232USBCON.M4 (S4), GND-CHK.1, GND-CHK1.1, GNSS-SP1.P$2 (2), GNSS-SP2.P$2 (2), IC5.7 (GND), IC5.18 (GND), IC5.21 (GND), IC5.25 (GND), IC5.26 (TEST), IIC1.P$1 (1), IIC2.P$1 (1), IIC3.P$1 (1), IIC4.P$1 (1), INTUART.3, JTAG.2, JTAG.10, K.1, K0.1, K1.1, K2.1, K3.1, K4.1, K5.1, K6.1, L6480.8, LCD.2, LCD.8, LCD-I2C.5, MEGA1.3 (GND), MEGA1.5 (GND), MEGA1.21 (GND), MEGA1-C1.1, MEGA2.3 (GND), MEGA2.5 (GND), MEGA2.21 (GND), MEGA2-C1.2, MOTOR-SUPPLY.2, MOTORDRIVER.13, MPU9250.10, PAD2.1, PING0.1, PING1.1, PING2.1, PING3.1, PING4.1, POWER-LED.C, Q1.2 (VSS), Q2.2 (VSS), RESET-MEGA1.3, RESET-MEGA1.4, RESET-MEGA2.3, RESET-MEGA2.4, RESET-XMEGA.3, RESET-XMEGA.4, RO1.P$1 (1), RO2.P$1 (1), SPI4.5, SPI5.5, SPI6.5, SPI7.5, SUOPPLY-SW1.P$2 (2), SUPPLY.2, SUPPLY3.3V.2, SUPPLY5V.2, SV3.6, SW6-R.1, SW7-R.1, TEST-R.1, U1.3 (GND), U1.13 (GND), U1.23 (GND), U1.33 (GND), U1.43 (GND), U1.53 (GND), U1.63 (GND), U1.73 (GND), U1.84 (GND), U1.93 (GND), VOL-LED.P$2 (2), VOLTAGE-METER.P$2 (2), X1.2, XMEGA-C1.2
INA: FALLING.2, U1.85 (PQ0)
INB: FALLING.3, U1.86 (PQ1)
L6480_STBY: L6480.10, U1.36 (PE1)
M1CS: MEGA2.25 (PC2(ADC2)), MOTORDRIVER.6, SS-2.2
M1EN: MEGA2.28 (PC5(ADC5/SCL)), MOTORDRIVER.10
M1INA: MEGA2.27 (PC4(ADC4/SDA)), MOTORDRIVER.9
M1INB: MEGA2.26 (PC3(ADC3)), MOTORDRIVER.8
M1PWM: MEGA2.10 (PD6(AIN0)), MOTORDRIVER.7
M2CS: MEGA1.25 (PC2(ADC2)), MOTORDRIVER.1, SS-1.2
M2EN: MEGA1.28 (PC5(ADC5/SCL)), MOTORDRIVER.5
M2INA: MEGA1.27 (PC4(ADC4/SDA)), MOTORDRIVER.4
M2INB: MEGA1.26 (PC3(ADC3)), MOTORDRIVER.3
M2PWM: MEGA1.10 (PD6(AIN0)), MOTORDRIVER.2
MISO: IC5.11 (!CTS), MEGA1.16 (PB4(MISO)), MEGA2.16 (PB4(MISO)), SPI-SW1.2
MISO-X: SPI-SW1.5, U1.21 (PC6)
MISO_E: L6480.3, MPU9250.5, U1.41 (PE6)
MISO_F: GNSSSPI.3, U1.51 (PF6)
MISO_U: LCD.1, SPI4.2, SPI5.2, SPI6.2, SPI7.2, U1.31 (PD6)
MOSI: IC5.10 (!DCD), MEGA1.15 (PB3(MOSI/OC2)), MEGA2.15 (PB3(MOSI/OC2)), SPI-SW1.1
MOSI-X: SPI-SW1.6, U1.20 (PC5)
MOSI_E: L6480.6, MPU9250.4, U1.40 (PE5)
MOSI_F: GNSSSPI.4, U1.50 (PF5)
MOSI_U: LCD.4, SPI4.1, SPI5.1, SPI6.1, SPI7.1, U1.30 (PD5)
M_PWM: FALLING.1, U1.35 (PE0)
unnamed: MEGA2.32 (PD2(INT0)), RO1.P$3 (3)
unnamed: POWER-LED.A, POWER-LEDR.1
unnamed: MEGA1.32 (PD2(INT0)), RO2.P$3 (3)
unnamed: M2-R2.2, Q3.S, SUPPLY.1, X1.1
unnamed: SV3.1, U1.89 (PDI)
unnamed: FT232-R6.1, IC5.15 (USBDP)
unnamed: MEGA1.7 (PB6(XTAL1/TOSC1)), Q1.1
unnamed: MEGA1.8 (PB7(XTAL2/TOSC2)), Q1.3
unnamed: FT232-R6.2, FT232USBCON.3
unnamed: FT232-R7.1, IC5.16 (USBDM)
unnamed: L6.A, U1.98 (PA3)
unnamed: L6.C, TEST-R.2
unnamed: MEGA2.7 (PB6(XTAL1/TOSC1)), Q2.1
unnamed: FT232-R7.2, FT232USBCON.2
unnamed: MEGA2.8 (PB7(XTAL2/TOSC2)), Q2.3
unnamed: FT232-R1.2, FT232USBCON.1, FT-POWERLED.A, IC5.20 (VCC)
unnamed: FT232-R1.1, FT232-R2.2, IC5.19 (!RESET)
unnamed: FT232-R4.2, L1.C
unnamed: FT232-R5.2, L2.C
unnamed: M2-R2.1, Q3.G, SUOPPLY-SW1.P$1 (1)
unnamed: IC5.4 (VCCIO), IC5.17 (3V3OUT)
unnamed: PING0.3, U1.55 (PH0)
unnamed: MOTOR-SUPPLY.1, MOTOR-SW.3 (S)
PH1: PING1.3, U1.56 (PH1)
PH2: PING2.3, U1.57 (PH2)
PH3: PING3.3, U1.58 (PH3)
PH4: PING4.3, U1.59 (PH4)
PH6: SW6.P$2 (2), SW6-R.2, U1.61 (PH6)
PH7: SW7.P$2 (2), SW7-R.2, U1.62 (PH7)
PK0: K0.2, TENKEY.8, U1.75 (PK0)
PK1: K1.2, TENKEY.7, U1.76 (PK1)
PK2: K2.2, TENKEY.6, U1.77 (PK2)
PK3: K3.2, TENKEY.5, U1.78 (PK3)
PK4: K4.2, TENKEY.4, U1.79 (PK4)
PK5: K5.2, TENKEY.3, U1.80 (PK5)
PK6: K6.2, TENKEY.2, U1.81 (PK6)
PK7: K.2, TENKEY.1, U1.82 (PK7)
RESET-M1: M1-R1.1, MEGA2.29 (PC6(/RESET)), RESET-MEGA2.1, RESET-MEGA2.2, S1.1
RESET-M2: M2-R1.1, MEGA1.29 (PC6(/RESET)), RESET-MEGA1.1, RESET-MEGA1.2, S1.2 (1)
RX0: INTUART.2, U1.37 (PE2)
RXD0_1: GNSSUART.2, U1.28 (PD3)
RXDM1: MEGA2.30 (PD0(RXD)), S1.6 (1)
RXDM2: MEGA1.30 (PD0(RXD)), S1.8 (1)
RXDX1: S1.4 (1), U1.17 (PC2)
SCK: IC5.9 (!DSR), MEGA1.17 (PB5(SCK)), MEGA2.17 (PB5(SCK)), SPI-SW1.3
SCK-X: SPI-SW1.4, U1.22 (PC7)
SCK_E: L6480.5, MPU9250.3, U1.42 (PE7)
SCK_F: GNSSSPI.2, U1.52 (PF7)
SCK_U: LCD.3, SPI4.3, SPI5.3, SPI6.3, SPI7.3, U1.32 (PD7)
SCL_D: IIC1.P$3 (3), IIC2.P$3 (3), IIC3.P$3 (3), IIC4.P$3 (3), IIC_D-R2.1, U1.26 (PD1)
SCL_F: IIC-UP2.2, LCD-I2C.3, U1.46 (PF1)
SDA_D: IIC1.P$4 (4), IIC2.P$4 (4), IIC3.P$4 (4), IIC4.P$4 (4), IIC_D-R.1, U1.25 (PD0)
SDA_F: IIC-UP1.2, LCD-I2C.4, U1.45 (PF0)
SS1: MEGA1.14 (PB2(SS/OC1B)), U1.15 (PC0)
SS2: MEGA2.14 (PB2(SS/OC1B)), U1.16 (PC1)
SS_F: U1.49 (PF4)
SS_U: LCD.7, SS-3.1, U1.29 (PD4)
TCK: JTAG.1, U1.11 (PB6)
TDI: JTAG.9, U1.10 (PB5)
TDO: JTAG.3, U1.12 (PB7)
TMS: JTAG.5, U1.9 (PB4)
TX0: INTUART.1, U1.38 (PE3)
TXD0_1: GNSSUART.1, U1.27 (PD2)
TXDM1: MEGA2.31 (PD1(TXD)), S1.5 (1)
TXDM2: MEGA1.31 (PD1(TXD)), S1.7 (1)
TXDX1: S1.3 (1), U1.18 (PC3)
X-RESET: JTAG.6, LCD-I2C.2, RESET-XMEGA.1, RESET-XMEGA.2, SV3.5, U1.90 (!RESET!/PDI), X-R1.1

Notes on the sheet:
FT232RL
MOTOR-AREA
LCD
SWITCHING-SWITCH
Supply
FT232接続のUSARTを USARTD1からUSARTC0に変更
MPU9250
L6480
外出しUART
カラーLCD
GNSS-UART
GNSS-SPI
超音波
JTAG
超音波予備
電源ピン (予備電源含)
UI-SW
L6470_STBYをPJ7からPE1に変更

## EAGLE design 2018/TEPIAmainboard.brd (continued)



Board: 2 copper layers, 128.7 x 99.3 mm, 110 parts (17 on the bottom side), 106 nets.

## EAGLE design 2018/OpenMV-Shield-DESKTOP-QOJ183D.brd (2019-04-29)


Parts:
L1: SP-L; CHIPLED_0805
L2: LED; CHIPLED_0805
LED-R: 330; R0805
MV1: B7B-ZR
SERMO: MA04-1
SP-R: 330; R0805
SV1, SV2: MA08-1
SW: MA03-1

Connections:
+3V3: SERMO.1, SV2.1
+5V: L1.A, SV1.2, SW.3
BOOT: SV1.7
GND: LED-R.1, MV1.7, SERMO.2, SP-R.1, SV1.1
MISOD: MV1.3, SV2.7
MOSID: MV1.2, SV2.8
MV: MV1.1, SV1.5
MVS: MV1.5, SV2.5
unnamed: MV1.6, SW.2
unnamed: L2.C, LED-R.2
unnamed: L1.C, SP-R.2
P4: SERMO.3, SV2.4
P5: SERMO.4, SV2.3
P6: SV2.2
P7: SV1.3
P8: L2.A, SV1.4
RST: SV1.8
SCKD: MV1.4, SV2.6
SYN: SV1.6

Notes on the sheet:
P0:PB15/MOSI P1:PB14/MISO P2:PB13/SCLK P3:PB12/SS P4:PB10/TXD/SCL P5:PB11/RXD/SDA P6:PA5/ADC/DAC P7:PD12/SERVO1 P8:PD13/SERVO2 P9:PD14/SERVO3



Board: 2 copper layers, 36.8 x 23.3 mm, 10 parts (2 on the bottom side), 14 nets.

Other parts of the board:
U$1: EAGLE-PLC-8MM

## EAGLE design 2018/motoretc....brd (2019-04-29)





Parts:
3.3C1, 3.3C6, 5C11, 5C16: 100u; E2,5-6
3.3C2, 3.3C3, 3.3C4, 3.3C5, 5C12, 5C13, 5C14, 5C15: 0.1u; C0805
3.3V-REGU, 5V-REGU: 78XXS
CHECKLED: OSTA71A1D-A
CN2: COLOR-XH-M; CON8
DEVEL: FE05-2
DEVEL-R1, DEVEL-R2: 4.7K; R0805
ERROR1-R, ERROR2-R: 330; R0805
FAN-GND: WIREPADSMD1,27-254; SMD1,27-2,54
FAN-VCC: WIREPADSMD1,27-254; SMD1,27-2,54
FT232-R1: 4.7K; R0805
FT232-R2: 10K; R0805
FT232-R3: 1K; R0805
FT232-R4, FT232-R5, FT234-R1, FT234-R2: 330; R0805
FT232-R6, FT232-R7: 23; R0805
FT232USBCON: Wrie-USB; 32005-201
FT234X: XH-4; CON4
FT-POWERLED: LEDCHIPLED_0805; CHIPLED_0805
GND-CHK, GND-CHK1: 2,15/1,0
I2CLCD: MA07-2
IC5: FT232RL; SSOP28
KK1, KK2: D01PA
L1: RXDLED; CHIPLED_0805
L2: TXDLED; CHIPLED_0805
L3: E1; LED5MM
L4: E2; LED5MM
LCD-I2C: LCD-I2C; MA05-1
LED-R1: 330; R0805
M1-R1, M2-R1, M2-R2: 4.7K; R0805
MAIN-LED, MAIN-LED1: XH-2; CON2
MEGA1, MEGA2: MEGA8-AI; TQFP32-08
MEGA1-C1, MEGA2-C1: 0.1u; C0805
MOTOR-SUPPLY: MOTOR; AK500/2
MOTOR-SW: 320-916
MOTORDRIVER: MA13-1
PAD2: SMD5; SMD2,54-5,08
POWER-LED: LEDCHIPLED_0805; CHIPLED_0805
POWER-LEDR: 1K; R0805
Q1, Q2: 20MHz; CSTLS_X
Q3: IRF9530; TO220BV
R150: 330; R0805
RESET-MEGA1: R-1; DTS-6
RESET-MEGA2: R-2; DTS-6
RESET-XMEGA: DTS-6
RO1, RO2: XH-3; CON3
RXD-LED1: RXDLED; CHIPLED_0805
S1: DIP08S
SCK-CHK: 2,15/1,0
SERMO: 0.1u; C0805
SERMO1, SERMO2: XH-4; CON4
SPI-SW: DIP03YL
SUOPPLY-SW1: XH-3; CON3
SUPPLY: MAIN; AK500/2
SV1: Range1; MA03-1
SV2: Range2; MA03-1
SV3: ML6
SV4: Range3; MA03-1
SV5: Range4; MA03-1
SV6: Range5; MA03-1
SV7: Range6; MA03-1
SV8: Servo; MA03-1
SW-LED: XH-4; CON4
SW-R1: 330; R0805
SW-R2, SW-R3, SW-R4: 4.7K; R0805
SW-RED: XH-4; CON4
TESTSW-R1, TESTSW-R2: 4.7K; R0805
TOUCH1, TOUCH2: XH-3; CON3
TXD-LED1: TXDLED; CHIPLED_0805
U1: ATXMEGA128A1U-AU; TQFP-100A-100
VOLTAGE-METER: XH-2; CON2
X1: DCJACK-MJ179P; MJ-179P
X-R1: 4.7K; R0805
XMEGA-C1: 0.1u; C0805
XMEGA-TEST1: SW1; DTS-6
XMEGA-TEST2: SW2; DTS-6

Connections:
+3V3: 3.3C4.1, 3.3C5.1, 3.3C6.+, 3.3V-REGU.OUT, CN2.P$1 (1), DEVEL.6, DEVEL.7, DEVEL.8, DEVEL.9, DEVEL.10, I2CLCD.2, LCD-I2C.1, M1-R1.2, M2-R1.2, MEGA1.4 (VCC), MEGA1.6 (VCC), MEGA1.18 (AVCC), MEGA1-C1.2, MEGA2.4 (VCC), MEGA2.6 (VCC), MEGA2.18 (AVCC), MEGA2-C1.1, MOTORDRIVER.11, R150.2, SERMO.2, SERMO1.P$2 (2), SERMO2.P$2 (2), SW-R2.1, SW-R3.2, SW-R4.2, SW-RED.P$2 (2), TOUCH1.P$2 (2), TOUCH2.P$2 (2), U1.4 (AVCC), U1.14 (VCC), U1.24 (VCC), U1.34 (VCC), U1.44 (VCC), U1.54 (VCC), U1.64 (VCC), U1.74 (VCC), U1.83 (VCC), U1.94 (AVCC), X-R1.2, XMEGA-C1.1, XMEGA-TEST1.1, XMEGA-TEST1.2, XMEGA-TEST2.1, XMEGA-TEST2.2
+5V: 5C14.1, 5C15.1, 5C16.+, 5V-REGU.OUT, CN2.P$7 (7), FAN-VCC.1, POWER-LEDR.2, RO1.P$2 (2), RO2.P$2 (2), SV1.2, SV2.2, SV4.2, SV5.2, SV6.2, SV7.2, SV8.2
+9V: 3.3C1.+, 3.3C2.1, 3.3C3.1, 3.3V-REGU.IN, 5C11.+, 5C12.1, 5C13.1, 5V-REGU.IN, MAIN-LED.P$1 (1), MOTOR-SW.2, MOTORDRIVER.12, Q3.D, VOLTAGE-METER.P$1 (1)
CK: CN2.P$5 (5), U1.66 (PJ1)
DEVEL1: DEVEL.1, DEVEL.3, DEVEL.5, DEVEL-R1.2, U1.72 (PJ7)
DEVEL2: DEVEL.2, DEVEL.4, DEVEL-R2.2, U1.71 (PJ6)
DOUT: CN2.P$3 (3), U1.68 (PJ3)
FT232-RXD: IC5.5 (RXD), L1.A, S1.10 (2), S1.12 (2), S1.14 (2)
FT232-TXD: IC5.1 (TXD), L2.A, S1.9 (2), S1.11 (2), S1.13 (2)
FT-POWERLED: FT232-R3.2, FT-POWERLED.C
FT-RESET: IC5.6 (!RI), LCD-I2C.2, RESET-XMEGA.1, RESET-XMEGA.2, S1.15 (2), S1.16 (2), SV3.5, U1.90 (!RESET!/PDI), X-R1.1
GATE: CN2.P$4 (4), U1.67 (PJ2)
GND: 3.3C1.-, 3.3C2.2, 3.3C3.2, 3.3C4.2, 3.3C5.2, 3.3C6.-, 3.3V-REGU.GND, 5C11.-, 5C12.2, 5C13.2, 5C14.2, 5C15.2, 5C16.-, 5V-REGU.GND, CN2.P$2 (2), DEVEL-R1.1, DEVEL-R2.1, ERROR1-R.1, ERROR2-R.1, FAN-GND.1, FT232-R2.1, FT232-R3.1, FT232-R4.1, FT232-R5.1, FT232USBCON.5, FT232USBCON.M1 (S1), FT234-R1.1, FT234-R2.1, FT234X.P$3 (3), GND-CHK.1, GND-CHK1.1, I2CLCD.1, IC5.7 (GND), IC5.18 (GND), IC5.21 (GND), IC5.25 (GND), IC5.26 (TEST), LCD-I2C.5, MAIN-LED.P$2 (2), MAIN-LED1.P$2 (2), MEGA1.3 (GND), MEGA1.5 (GND), MEGA1.21 (GND), MEGA1-C1.1, MEGA2.3 (GND), MEGA2.5 (GND), MEGA2.21 (GND), MEGA2-C1.2, MOTOR-SUPPLY.2, MOTORDRIVER.13, PAD2.1, POWER-LED.C, Q1.2 (VSS), Q2.2 (VSS), RESET-MEGA1.3, RESET-MEGA1.4, RESET-MEGA2.3, RESET-MEGA2.4, RESET-XMEGA.3, RESET-XMEGA.4, RO1.P$1 (1), RO2.P$1 (1), SERMO.1, SERMO1.P$1 (1), SERMO2.P$1 (1), SUOPPLY-SW1.P$2 (2), SUPPLY.2, SV1.1, SV2.1, SV3.6, SV4.1, SV5.1, SV6.1, SV7.1, SV8.1, SW-LED.P$1 (1), SW-LED.P$3 (3), SW-RED.P$3 (3), TESTSW-R1.1, TESTSW-R2.1, TOUCH1.P$3 (3), TOUCH2.P$3 (3), U1.3 (GND), U1.13 (GND), U1.23 (GND), U1.33 (GND), U1.43 (GND), U1.53 (GND), U1.63 (GND), U1.73 (GND), U1.84 (GND), U1.93 (GND), VOLTAGE-METER.P$2 (2), X1.2, XMEGA-C1.2
LED1: LED-R1.2, U1.28 (PD3)
M1CS: MEGA2.25 (PC2(ADC2)), MOTORDRIVER.6
M1EN: MEGA2.28 (PC5(ADC5/SCL)), MOTORDRIVER.10
M1INA: MEGA2.27 (PC4(ADC4/SDA)), MOTORDRIVER.9
M1INB: MEGA2.26 (PC3(ADC3)), MOTORDRIVER.8
M1PWM: MEGA2.10 (PD6(AIN0)), MOTORDRIVER.7
M2CS: MEGA1.25 (PC2(ADC2)), MOTORDRIVER.1
M2EN: MEGA1.28 (PC5(ADC5/SCL)), MOTORDRIVER.5
M2INA: MEGA1.27 (PC4(ADC4/SDA)), MOTORDRIVER.4
M2INB: MEGA1.26 (PC3(ADC3)), MOTORDRIVER.3
M2PWM: MEGA1.10 (PD6(AIN0)), MOTORDRIVER.2
MISO: MEGA1.16 (PB4(MISO)), MEGA2.16 (PB4(MISO)), SCK-CHK.1, SPI-SW.6, U1.21 (PC6)
MOSI: MEGA1.15 (PB3(MOSI/OC2)), MEGA2.15 (PB3(MOSI/OC2)), SPI-SW.4, U1.20 (PC5)
unnamed: SV1.3, U1.60 (PH5)
unnamed: MEGA2.32 (PD2(INT0)), RO1.P$3 (3)
unnamed: SV2.3, U1.76 (PK1)
unnamed: POWER-LED.A, POWER-LEDR.1
unnamed: MEGA1.32 (PD2(INT0)), RO2.P$3 (3)
unnamed: M2-R2.2, Q3.S, SUPPLY.1, X1.1
unnamed: SV3.1, U1.89 (PDI)
unnamed: FT232-R6.1, IC5.15 (USBDP)
unnamed: MEGA1.7 (PB6(XTAL1/TOSC1)), Q1.1
unnamed: MEGA1.8 (PB7(XTAL2/TOSC2)), Q1.3
unnamed: FT232-R6.2, FT232USBCON.3
unnamed: FT234-R2.2, RXD-LED1.C
unnamed: FT232-R7.1, IC5.16 (USBDM)
unnamed: CHECKLED.ANODE, R150.1
unnamed: FT234-R1.2, TXD-LED1.C
unnamed: IC5.11 (!CTS), SPI-SW.1
unnamed: SW-LED.P$2 (2), SW-R1.1
unnamed: MEGA2.7 (PB6(XTAL1/TOSC1)), Q2.1
unnamed: LED-R1.1, MAIN-LED1.P$1 (1)
unnamed: IC5.9 (!DSR), SPI-SW.2
unnamed: FT232-R7.2, FT232USBCON.2
unnamed: MEGA2.8 (PB7(XTAL2/TOSC2)), Q2.3
unnamed: FT232-R1.2, FT232USBCON.1, FT-POWERLED.A, IC5.20 (VCC)
unnamed: FT232-R1.1, FT232-R2.2, IC5.19 (!RESET)
unnamed: FT232-R4.2, L1.C
unnamed: FT232-R5.2, L2.C
unnamed: M2-R2.1, Q3.G, SUOPPLY-SW1.P$1 (1)
unnamed: IC5.10 (!DCD), SPI-SW.3
unnamed: IC5.4 (VCCIO), IC5.17 (3V3OUT)
unnamed: MOTOR-SUPPLY.1, MOTOR-SW.3 (S)
unnamed: ERROR1-R.2, L3.K (C)
unnamed: ERROR2-R.2, L4.K (C)
PA6: U1.1 (PA6)
PA7: U1.2 (PA7)
PC7: SV5.3, U1.27 (PD2)
PD4: SW-R1.2, U1.29 (PD4)
PD5: SW-LED.P$4 (4), SW-R2.2, U1.30 (PD5)
PE0: SW-RED.P$1 (1), U1.35 (PE0)
PE2: SV6.3, U1.37 (PE2)
PE3: SV7.3, U1.38 (PE3)
PE4: L4.A, U1.39 (PE4)
PE5: L3.A, U1.40 (PE5)
PF5: U1.50 (PF5)
PF6: TESTSW-R2.2, U1.51 (PF6), XMEGA-TEST2.3, XMEGA-TEST2.4
PF7: TESTSW-R1.2, U1.52 (PF7), XMEGA-TEST1.3, XMEGA-TEST1.4
PH2: CHECKLED.RED, U1.57 (PH2)
PH3: CHECKLED.GREEN, U1.58 (PH3)
PH4: CHECKLED.BLUE, U1.59 (PH4)
PH6: U1.61 (PH6)
PH7: U1.62 (PH7)
PJ0: TOUCH1.P$1 (1)
PJ4: I2CLCD.4, U1.69 (PJ4)
PJ5: TOUCH2.P$1 (1), U1.70 (PJ5)
PK5: SV4.3, U1.80 (PK5)
RANGE: CN2.P$6 (6), U1.65 (PJ0)
RESET-M1: M1-R1.1, MEGA2.29 (PC6(/RESET)), RESET-MEGA1.1, RESET-MEGA1.2, S1.1
RESET-M2: M2-R1.1, MEGA1.29 (PC6(/RESET)), RESET-MEGA2.1, RESET-MEGA2.2, S1.2 (1)
RXDM1: MEGA2.30 (PD0(RXD)), S1.6 (1)
RXDM2: MEGA1.30 (PD0(RXD)), S1.8 (1)
RXDX1: S1.4 (1), U1.17 (PC2)
RXDX2: FT234X.P$2 (2), TXD-LED1.A, U1.47 (PF2)
SCK: MEGA1.17 (PB5(SCK)), MEGA2.17 (PB5(SCK)), SPI-SW.5, U1.22 (PC7)
SCL_C: SERMO1.P$3 (3), U1.16 (PC1)
SCL_D: SERMO2.P$3 (3), U1.26 (PD1)
SCL_F: I2CLCD.7, LCD-I2C.3, SW-R3.1, U1.46 (PF1)
SDA_C: SERMO1.P$4 (4), U1.15 (PC0)
SDA_D: SERMO2.P$4 (4), U1.25 (PD0)
SDA_F: I2CLCD.8, I2CLCD.9, LCD-I2C.4, SW-R4.1, U1.45 (PF0)
SERVO: SV8.3, U1.100 (PA5)
SS1: MEGA1.14 (PB2(SS/OC1B)), U1.11 (PB6)
SS2: MEGA2.14 (PB2(SS/OC1B)), U1.12 (PB7)
TXDM1: MEGA2.31 (PD1(TXD)), S1.5 (1)
TXDM2: MEGA1.31 (PD1(TXD)), S1.7 (1)
TXDX1: S1.3 (1), U1.18 (PC3)
TXDX2: FT234X.P$1 (1), RXD-LED1.A, U1.48 (PF3)

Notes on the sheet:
ping
FT232RL
SERMO
MOTOR-AREA
LCD
TOUCH
COLOR-XH-mother
SWITCHING-SWITCH
MAIN-LED
DEVEL-SENSER
CHECK-SW
FT234X
CHECK-LED
Serial-LED
Supply
ServoMotor
ERROR-LEDs
Xmega-TESTSW



Board: 2 copper layers, 128.7 x 99.3 mm, 109 parts (4 on the bottom side), 95 nets.

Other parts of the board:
U$2: I2C
U$3: LOGO
U$4: EAGLE-PLC-10MM

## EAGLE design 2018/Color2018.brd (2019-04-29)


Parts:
CN2: COLOR-ZH-M; B7B-ZR
LED1: GM1WA55311A
R1, R5, R6: 330; R0805
U$1: S9706

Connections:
+3V3: CN2.1, U$1.VDD
+5V: CN2.7, LED1.4 (A)
CK: CN2.5, U$1.CK
DOUT: CN2.3, U$1.DOUT
GATE: CN2.4, U$1.GATE
GND: CN2.2, R1.1, R5.1, R6.1, U$1.GND
unnamed: LED1.2 (CRED), R1.2
unnamed: LED1.3 (CBLUE), R5.2
unnamed: LED1.1 (CGREEN), R6.2
RANGE: CN2.6, U$1.RANGE



Board: 2 copper layers, 17.8 x 17.4 mm, 7 parts (2 on the bottom side), 10 nets.

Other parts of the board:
U$2: EAGLE-PLC-8MM

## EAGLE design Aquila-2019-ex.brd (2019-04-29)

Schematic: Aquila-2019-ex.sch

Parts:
3.3C1, 5C1, 9C1: 100u; D/7343-31R
3.3C2, 5C2, 9C2: 0.1u; C0805
3.3REG, 5VREG: OKL-T_6-W12N-C; OKL-T/3-W5
8MHZ: P-08669_HUSG-12.000-20; HC49U-V
BOOT0-STM: DTS-6
C1, C3: 22uF25V; C2012
C2, C4: 10uF10V; C2012
C5, C6: 22pF; C1608
CHECKLED: OSTA71A1D-A
CON1, CON2: XH-4; CON4
DIO0-JP: BOOT0; SJ
DIO1-JP: NRST; SJ
ERROR1-R, ERROR2-R: 330; R0805
FET1, FET2: IRF740; TO220BV
FET1-R1, FET2-R1: 100; R0805
FET1-R2, FET2-R2: 4.7K; R0805
GND-CH: GND; SMD2,54-5,08
GND-CHK, GND-CHK1: GND; 2,15/1,0
I2C-R1, I2C-R2: 4.7k; R0805
IC1: STM32F429VGT; LQFP100
IC2: ULN2003AN; DIL16
IC3: AT24CP; DIL08
IC4: AE-AQM0802
IIC-R: XH-4; CON4
INDILED1, INDILED2, INDILED3, INDILED4: 330; R0805
J1: XH-5; CON5
JY901: XH-4; CON4
L3: E1; LED5MM
L4: E2; LED5MM
LED1, LED2: OSL10564-CD4026B-R; DIPS1524W50P254L1260H800Q10N
LEDSP, LEDSP2: MAIN; AK500/2
M-SW: TL36PO; TL3XPO
MAIN-SPL: XH-2; CON2
MAINSW2: MAIN; MA03-1
MOTORDRIVER: MDCON; ML14
Q3, Q4, Q5: IRF9530; TO220BV
R1, R2: 1.2k; 0204/7
R-B: ?; R0805
R-G: ?; R0805
R-R: ?; R0805
RESET-STM: DTS-6
S1, S3: SKRPACE010; SW_SKRPACE010
S2: VM; M251
SG1: F/EE17P
SL-R1: 1K; R0805
SP-LED: LEDCHIPLED_0805; CHIPLED_0805
SP-R1, SP-R3: 1.2k; R0805
SP-R2, SP-R4: 20K; R0805
SP-R5, SP-R6: 4.7K; R0805
SP-RC1, SP-RC2: 20k; RTRIM3296W
SP-SW2: 219-02; CTS-219-02
SPI-LCD: FE09-1; FE09
SPI-R: XH-6; CON6
SRAM-R1: 4.7K; R0805
SRAM-R2: 10k; R0805
STEPINDI1, STEPINDI2, STEPINDI3, STEPINDI4: LED; CHIPLED_0805
STM-C1, STM-C2, STM-C3, STM-C4, STM-C5, STM-C6: 0.1u; C0805
STM-R1, STM-R2: 4.7K; R0805
SUOPPLY-SW2: XH-3; CON3
SUPPLY3.3V, SUPPLY5V, SUPPLY9: MAIN; AK500/2
SV1: MA06-1
TESTSW-R1, TESTSW-R2, TESTSW-R3: 4.7K; R0805
TO-UNDER: ML26
TOUCH1, TOUCH2: XH-3; CON3
TW-SP: XH-2; CON2
TWILITE: C2; MA05-1
U2: 23K256-I/SN; SOIC127P600X175-8N
U$2: 5566-04A
VOLTAGE-METER1, VOLTAGE-METER2: XH-2; CON2
X2: DCJACK-MJ179P; MJ-179P
X-R2: 4.7K; R0805
XB1: XBEE-PRO
XBEE-RST: 4.7K; R0805
XMEGA-TEST1: SW1; DTS-6
XMEGA-TEST2: SW2; DTS-6
XMEGA-TEST3: SW3; DTS-6

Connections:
+3V3: 3.3C1.+, 3.3C2.1, 3.3REG.4 (VOUT), 3.3REG.5 (SENSE), BOOT0-STM.1, BOOT0-STM.2, C4.1, CHECKLED.ANODE, I2C-R1.2, I2C-R2.2, IC1.6 (VBAT), IC1.11 (VDD), IC1.19 (VDD), IC1.21 (VREF+), IC1.22 (VDDA), IC1.28 (VDD), IC1.50 (VDD), IC1.75 (VDD), IC1.100 (VDD), IC3.1 (A0), IC3.2 (A1), IC3.3 (A2), IC3.8 (VCC), IC4.VDD, IIC-R.P$3 (3), JY901.P$4 (4), LED1.1 (VDD), LED2.1 (VDD), MOTORDRIVER.11, R2.1, S2.1 (O), S3.3, S3.4, SPI-LCD.1, SPI-R.P$1 (1), SRAM-R1.2, SRAM-R2.2, STM-C1.2, STM-C2.2, STM-C3.2, STM-C4.2, STM-R1.2, SUPPLY3.3V.1, SV1.1, TO-UNDER.24, TOUCH1.P$2 (2), TOUCH2.P$2 (2), TW-SP.P$2 (2), U2.8 (VCC), U$2.4, XB1.1 (VCC), XB1.14 (VREF), XBEE-RST.2, XMEGA-TEST1.1, XMEGA-TEST1.2, XMEGA-TEST2.1, XMEGA-TEST2.2, XMEGA-TEST3.1, XMEGA-TEST3.2
+5V: 5C1.+, 5C2.1, 5VREG.4 (VOUT), 5VREG.5 (SENSE), C2.1, CON1.P$3 (3), CON2.P$3 (3), IC2.9 (CD+), INDILED1.2, INDILED2.2, INDILED3.2, INDILED4.2, J1.P$1 (1), R1.1, S2.3 (S), SP-LED.A, SUPPLY5V.1, U$2.3
+9V: 3.3REG.2 (VIN), 5VREG.2 (VIN), 9C1.+, 9C2.1, C1.1, C3.1, LEDSP.1, LEDSP2.1, MAIN-SPL.P$1 (1), Q4.S, Q5.D, SP-R2.2, SP-R4.2, SP-R5.2, VOLTAGE-METER1.P$1 (1)
BUZZER: IC1.77 (PA15), SG1.1, X-R2.2
CK: IC1.88 (PD7), TO-UNDER.6
CL: IC1.65 (PC8), LED1.9 (CL)
DIO0: BOOT0-STM.3, BOOT0-STM.4, DIO0-JP.1, IC1.94 (BOOT0), STM-R2.1
DIO1: DIO1-JP.1, IC1.14 (NRST), IC4.RESET, RESET-STM.3, RESET-STM.4, STM-R1.1, SV1.5
DOUT: IC1.90 (PB4), TO-UNDER.4
DP1: IC1.69 (PA10), LED1.5 (DP)
DP2: IC1.70 (PA11), LED2.5 (DP)
E1: IC1.35 (PB0), L3.A
E2: IC1.36 (PB1), L4.A
FET1: FET1-R1.2, IC1.95 (PB8)
FET2: FET2-R1.2, IC1.96 (PB9)
FLED-BLUE: IC1.7 (PC13), R-B.1
FLED-GREEN: IC1.8 (PC14), R-G.1
FLED-RED: IC1.9 (PC15), R-R.1
GATE: IC1.89 (PB3), TO-UNDER.5
GND: 3.3C1.-, 3.3C2.2, 3.3REG.3 (GND_1), 3.3REG.7 (GND_2), 5C1.-, 5C2.2, 5VREG.3 (GND_1), 5VREG.7 (GND_2), 9C1.-, 9C2.2, C1.2, C2.2, C3.2, C4.2, C5.1, C6.1, CON1.P$4 (4), CON2.P$4 (4), ERROR1-R.1, ERROR2-R.1, FET1.S, FET1-R2.1, FET2.S, FET2-R2.1, GND-CH.1, GND-CHK.1, GND-CHK1.1, IC1.10 (VSS), IC1.20 (VSSA), IC1.27 (VSS), IC1.74 (VSS), IC1.99 (VSS), IC2.5 (I5), IC2.6 (I6), IC2.7 (I7), IC2.8 (GND), IC3.4 (GND), IC3.7 (WP), IC4.GND, IIC-R.P$4 (4), JY901.P$1 (1), LED1.8 (GND), LED2.8 (GND), M-SW.3 (S), MAIN-SPL.P$2 (2), MAINSW2.2, MOTORDRIVER.13, Q3.G, R1.2, R2.2, RESET-STM.1, RESET-STM.2, S1.1, S1.2, SG1.2, SL-R1.1, SP-R1.1, SP-R3.1, SP-SW2.3, SP-SW2.4, SPI-LCD.2, SPI-LCD.8, SPI-R.P$6 (6), STM-C1.1, STM-C2.1, STM-C3.1, STM-C4.1, STM-C5.2, STM-C6.2, STM-R2.2, SUOPPLY-SW2.P$2 (2), SUPPLY3.3V.2, SUPPLY5V.2, SUPPLY9.2, SV1.3, TESTSW-R1.1, TESTSW-R2.1, TESTSW-R3.1, TOUCH1.P$3 (3), TOUCH2.P$3 (3), TW-SP.P$1 (1), U2.4 (VSS), U$2.2, VOLTAGE-METER1.P$2 (2), VOLTAGE-METER2.P$2 (2), X2.2, X-R2.1, XB1.10 (GND)
LCD-CS: IC1.53 (PB14), SPI-LCD.3
LCD-RST: IC1.54 (PB15), SPI-LCD.4
LED-RST: IC1.71 (PA12), LED1.2 (RS), LED2.2 (RS), S3.1, S3.2
M1CS: IC1.41 (PE10), MOTORDRIVER.6
M1EN: IC1.38 (PE7), MOTORDRIVER.10
M1INA: IC1.37 (PB2), MOTORDRIVER.9
M1INB: IC1.39 (PE8), MOTORDRIVER.8
M1PWM: IC1.40 (PE9), MOTORDRIVER.7
M2CS: IC1.46 (PE15), MOTORDRIVER.1
M2EN: IC1.43 (PE12), MOTORDRIVER.5
M2INA: IC1.44 (PE13), MOTORDRIVER.4
M2INB: IC1.45 (PE14), MOTORDRIVER.3
M2PWM: IC1.42 (PE11), MOTORDRIVER.2
MISOD: IC1.17 (PC2), TO-UNDER.15
MISOF: IC1.31 (PA6), SPI-LCD.9, SPI-R.P$4 (4), U2.2 (SO)
MOSID: IC1.18 (PC3), TO-UNDER.16
MOSIF: IC1.32 (PA7), SPI-LCD.6, SPI-R.P$3 (3), U2.5 (SI)
MR1A: CON1.P$2 (2), IC1.23 (PA0)
MR1B: CON1.P$1 (1), IC1.24 (PA1)
MR2A: CON2.P$2 (2), IC1.63 (PC6)
MR2B: CON2.P$1 (1), IC1.64 (PC7)
MV1: IC1.78 (PC10), TO-UNDER.19
MV2: IC1.79 (PC11), TO-UNDER.18
MV3: IC1.80 (PC12), TO-UNDER.17
MVS1: IC1.3 (PE4), TO-UNDER.1
MVS2: IC1.2 (PE3), TO-UNDER.2
MVS3: IC1.1 (PE2), TO-UNDER.3
unnamed: IC1.62 (PD15), IC2.4 (I4)
unnamed: DIO1-JP.2, XB1.19 (AD1/DIO1)
unnamed: SP-R1.2, SP-RC1.1 (A), SP-RC1.2 (S)
unnamed: IC1.61 (PD14), IC2.3 (I3)
unnamed: Q3.S, Q5.S, SP-R6.2
unnamed: Q4.D, U$2.1
unnamed: SP-R3.2, SP-RC2.1 (A), SP-RC2.2 (S)
unnamed: M-SW.2, Q4.G
unnamed: 5VREG.6 (TRIM), SP-RC1.3 (E)
unnamed: M-SW.1 (O), SP-R5.1
unnamed: S2.2, VOLTAGE-METER2.P$1 (1)
unnamed: IC1.60 (PD13), IC2.2 (I2)
unnamed: 3.3REG.6 (TRIM), SP-RC2.3 (E)
unnamed: IC1.59 (PD12), IC2.1 (I1)
unnamed: 3.3REG.1 (ON/OFF), SP-R4.1, SP-SW2.2
unnamed: IC2.16 (O1), J1.P$2 (2), STEPINDI1.C
unnamed: IC2.15 (O2), J1.P$3 (3), STEPINDI2.C
unnamed: IC2.14 (O3), J1.P$4 (4), STEPINDI3.C
unnamed: IC2.13 (O4), J1.P$5 (5), STEPINDI4.C
unnamed: INDILED4.1, STEPINDI4.A
unnamed: INDILED3.1, STEPINDI3.A
unnamed: INDILED2.1, STEPINDI2.A
unnamed: INDILED1.1, STEPINDI1.A
unnamed: SL-R1.2, SP-LED.C
unnamed: 8MHZ.1, C6.2, IC1.13 (OSC_OUT)
unnamed: 5VREG.1 (ON/OFF), SP-R2.1, SP-SW2.1
unnamed: 8MHZ.2, C5.2, IC1.12 (OSC_IN)
unnamed: FET1.G, FET1-R1.1, FET1-R2.2
unnamed: FET1.D, LEDSP.2
unnamed: FET2.G, FET2-R1.1, FET2-R2.2
unnamed: FET2.D, LEDSP2.2
unnamed: IC1.73 (VCAP2), STM-C5.1
unnamed: IC1.49 (VCAP1), STM-C6.1
unnamed: Q3.D, SUPPLY9.1, X2.1
unnamed: DIO0-JP.2, XB1.20 (AD0/DIO0)
unnamed: MAINSW2.1, Q5.G, SP-R6.1, SUOPPLY-SW2.P$1 (1)
unnamed: S1.3, S1.4, XB1.5 (!RESET), XBEE-RST.1
unnamed: ERROR1-R.2, L3.K (C)
unnamed: ERROR2-R.2, L4.K (C)
unnamed: LED1.4 (CO), LED2.9 (CL)
unnamed: CHECKLED.RED, R-R.2
unnamed: CHECKLED.GREEN, R-G.2
unnamed: CHECKLED.BLUE, R-B.2
PING1: IC1.81 (PD0), TO-UNDER.13
PING2: IC1.82 (PD1), TO-UNDER.12
PING3: IC1.83 (PD2), TO-UNDER.11
PING4: IC1.84 (PD3), TO-UNDER.10
PING5: IC1.85 (PD4), TO-UNDER.9
PING6: IC1.86 (PD5), TO-UNDER.8
RAM-CS: IC1.4 (PE5), SRAM-R1.1, U2.1 (~CS)
RAM-HOLD: IC1.29 (PA4), SRAM-R2.1, U2.7 (~HOLD)
RANGE: IC1.87 (PD6), TO-UNDER.7
RO1: TO-UNDER.25
RO2: TO-UNDER.26
SCKD: IC1.52 (PB13), TO-UNDER.14
SCKF: IC1.30 (PA5), SPI-LCD.7, SPI-R.P$2 (2), U2.6 (SCK)
SCL-C: I2C-R1.1, IC1.47 (PB10), IC3.6 (SCL), IIC-R.P$1 (1), JY901.P$2 (2)
SCL-D: IC1.67 (PA8), IC4.SCL, TO-UNDER.20
SDA-C: I2C-R2.1, IC1.48 (PB11), IC3.5 (SDA), IIC-R.P$2 (2), JY901.P$3 (3)
SDA-D: IC1.66 (PC9), IC4.SDA, TO-UNDER.21
SS-R: IC1.5 (PE6), SPI-R.P$5 (5)
SW1: IC1.55 (PD8), TESTSW-R1.2, XMEGA-TEST1.3, XMEGA-TEST1.4
SW2: IC1.56 (PD9), TESTSW-R2.2, XMEGA-TEST2.3, XMEGA-TEST2.4
SW3: IC1.57 (PD10), TESTSW-R3.2, XMEGA-TEST3.3, XMEGA-TEST3.4
SWCLK: IC1.76 (PA14), SV1.2
SWDIO: IC1.72 (PA13), SV1.4
TOUCH1: IC1.15 (PC0), TOUCH1.P$1 (1)
TOUCH2: IC1.16 (PC1), TOUCH2.P$1 (1)
USART1-RX: IC1.93 (PB7), XB1.2 (DOUT)
USART1-TX: IC1.92 (PB6), XB1.3 (DIN/!CONFIG)
USART2RX: IC1.26 (PA3), TWILITE.4
USART2TX: IC1.25 (PA2), TWILITE.2

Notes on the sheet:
CHECK-LED
Xmega-TESTSW
TOUCH
Buzzer
ERROR-LEDs
電源ピン (予備電源含)



Board: 2 copper layers, 99.0 x 98.7 mm, 123 parts (26 on the bottom side), 117 nets.

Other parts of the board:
U$1: EAGLE-PLC-12MM
U$3: I2C
U$4: TONNE_10.00
U$5: LOGO

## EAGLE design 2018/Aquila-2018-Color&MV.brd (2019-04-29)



Board: 2 copper layers, 77.0 x 88.0 mm, 96 parts (24 on the bottom side), 136 nets.

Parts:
CN5, CN6, CN7, CN8, CN9, CN10, CN11, CN12: COLOR-ZH-M; B7B-ZR
L1, L3, L5, L7: SP-L; CHIPLED_0805
L2, L4, L6, L8: LED; CHIPLED_0805
LED5, LED6, LED7, LED8, LED9, LED10, LED11, LED12: GM1WA55311A
LED-R, LED-R1, LED-R2, LED-R3: 330; R0805
MV1, MV2, MV3, MV4: B7B-ZR
R13, R14, R15, R16, R17, R18, R19, R20, R21, R22, R23, R24, R25, R26, R27, R28, R29, R30, R31, R32, R33, R34, R35, R36: 330; R0805
S1, S2, S3, S4: M251
SERMO, SERMO1, SERMO2, SERMO3: MA04-1
SP-R, SP-R1, SP-R2, SP-R3: 330; R0805
SV1, SV2, SV3, SV4, SV5, SV6, SV7, SV8: MA08-1
U$1, U$2, U$3, U$4, U$12, U$14, U$16, U$18, U$20, U$22, U$24, U$26: EAGLE-PLC-8MM
U$11, U$13, U$15, U$17, U$19, U$21, U$23, U$25: S9706

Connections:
+3V1: SERMO1.1, SV4.1
+3V2: SERMO2.1, SV6.1
+3V3: SERMO.1, SV2.1
+3V4: SERMO3.1, SV8.1
+3V7: CN9.1, U$11.VDD
+3V8: CN10.1, U$21.VDD
+3V9: CN5.1, U$13.VDD
+3V10: CN6.1, U$15.VDD
+3V11: CN7.1, U$17.VDD
+3V12: CN8.1, U$19.VDD
+3V13: CN11.1, U$23.VDD
+3V14: CN12.1, U$25.VDD
+5V: L1.A, S1.3, SV1.2
+5V1: L3.A, S2.3, SV3.2
+5V2: L5.A, S3.3, SV5.2
+5V3: L7.A, S4.3, SV7.2
+5V6: CN9.7, LED9.4
+5V7: CN10.7, LED10.4
+5V8: CN5.7, LED5.4
+5V9: CN6.7, LED6.4
+5V10: CN7.7, LED7.4
+5V11: CN8.7, LED8.4
+5V12: CN11.7, LED11.4
+5V13: CN12.7, LED12.4
CK4: CN5.5, U$13.CK
CK5: CN6.5, U$15.CK
CK6: CN7.5, U$17.CK
CK7: CN8.5, U$19.CK
CK8: CN9.5, U$11.CK
CK9: CN10.5, U$21.CK
CK10: CN11.5, U$23.CK
CK11: CN12.5, U$25.CK
DOUT4: CN5.3, U$13.DOUT
DOUT5: CN6.3, U$15.DOUT
DOUT6: CN7.3, U$17.DOUT
DOUT7: CN8.3, U$19.DOUT
DOUT8: CN9.3, U$11.DOUT
DOUT9: CN10.3, U$21.DOUT
DOUT10: CN11.3, U$23.DOUT
DOUT11: CN12.3, U$25.DOUT
GATE4: CN5.4, U$13.GATE
GATE5: CN6.4, U$15.GATE
GATE6: CN7.4, U$17.GATE
GATE7: CN8.4, U$19.GATE
GATE8: CN9.4, U$11.GATE
GATE9: CN10.4, U$21.GATE
GATE10: CN11.4, U$23.GATE
GATE11: CN12.4, U$25.GATE
GND: LED-R.1, MV1.7, SERMO.2, SP-R.1, SV1.1
GND1: LED-R1.1, MV2.7, SERMO1.2, SP-R1.1, SV3.1
GND2: LED-R2.1, MV3.7, SERMO2.2, SP-R2.1, SV5.1
GND3: LED-R3.1, MV4.7, SERMO3.2, SP-R3.1, SV7.1
GND6: CN9.2, R25.1, R26.1, R27.1, U$11.GND
GND7: CN10.2, R28.1, R29.1, R30.1, U$21.GND
GND8: CN5.2, R13.1, R14.1, R15.1, U$13.GND
GND9: CN6.2, R16.1, R17.1, R18.1, U$15.GND
GND10: CN7.2, R19.1, R20.1, R21.1, U$17.GND
GND11: CN8.2, R22.1, R23.1, R24.1, U$19.GND
GND12: CN11.2, R31.1, R32.1, R33.1, U$23.GND
GND13: CN12.2, R34.1, R35.1, R36.1, U$25.GND
MISOD: MV1.3, SV2.7
MISOD1: MV2.3, SV4.7
MISOD2: MV3.3, SV6.7
MISOD3: MV4.3, SV8.7
MOSID: MV1.2, SV2.8
MOSID1: MV2.2, SV4.8
MOSID2: MV3.2, SV6.8
MOSID3: MV4.2, SV8.8
MV: MV1.1, SV1.5
MV1: MV2.1, SV3.5
MV2: MV3.1, SV5.5
MV3: MV4.1, SV7.5
MVS: MV1.5, SV2.5
MVS1: MV2.5, SV4.5
MVS2: MV3.5, SV6.5
MVS3: MV4.5, SV8.5
unnamed: MV1.6, S1.2
unnamed: L2.C, LED-R.2
unnamed: MV2.6, S2.2
unnamed: L3.C, SP-R1.2
unnamed: L4.C, LED-R1.2
unnamed: MV3.6, S3.2
unnamed: L5.C, SP-R2.2
unnamed: L6.C, LED-R2.2
unnamed: MV4.6, S4.2
unnamed: L7.C, SP-R3.2
unnamed: L8.C, LED-R3.2
unnamed: LED9.2, R25.2
unnamed: LED9.3, R26.2
unnamed: LED9.1, R27.2
unnamed: LED10.2, R28.2
unnamed: LED5.2, R13.2
unnamed: LED5.3, R14.2
unnamed: LED5.1, R15.2
unnamed: LED6.2, R16.2
unnamed: LED6.3, R17.2
unnamed: LED6.1, R18.2
unnamed: LED7.2, R19.2
unnamed: LED7.3, R20.2
unnamed: L1.C, SP-R.2
unnamed: LED7.1, R21.2
unnamed: LED8.2, R22.2
unnamed: LED8.3, R23.2
unnamed: LED8.1, R24.2
unnamed: LED10.3, R29.2
unnamed: LED10.1, R30.2
unnamed: LED11.2, R31.2
unnamed: LED11.3, R32.2
unnamed: LED11.1, R33.2
unnamed: LED12.2, R34.2
unnamed: LED12.3, R35.2
unnamed: LED12.1, R36.2
P1: L4.A, SV3.4
P3: SERMO1.3, SV4.4
P4: SERMO.3, SV2.4
P5: SERMO.4, SV2.3
P8: L2.A, SV1.4
P9: SERMO1.4, SV4.3
P11: L6.A, SV5.4
P13: SERMO2.3, SV6.4
P14: SERMO2.4, SV6.3
P16: L8.A, SV7.4
P18: SERMO3.3, SV8.4
P19: SERMO3.4, SV8.3
RANGE4: CN5.6, U$13.RANGE
RANGE5: CN6.6, U$15.RANGE
RANGE6: CN7.6, U$17.RANGE
RANGE7: CN8.6, U$19.RANGE
RANGE8: CN9.6, U$11.RANGE
RANGE9: CN10.6, U$21.RANGE
RANGE10: CN11.6, U$23.RANGE
RANGE11: CN12.6, U$25.RANGE
SCKD: MV1.4, SV2.6
SCKD1: MV2.4, SV4.6
SCKD2: MV3.4, SV6.6
SCKD3: MV4.4, SV8.6
